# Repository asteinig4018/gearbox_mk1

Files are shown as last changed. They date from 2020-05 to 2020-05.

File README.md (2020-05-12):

# Gearbox Project (featuring snap fits)

Just a simple 3D printed gearbox to be used with my TM 9V Arduino kit motor. Gears down the high speed to a potentiometer - compatible speed.

## Motivation

I wanted to use a 9V TM motor with a 10K ACP Potentiometer (180 degrees of rotation). 
I was hopping to put something physical with the Arduino PID library. 
I also wanted to explore 3D printed snap fits and gears.
And, finally, write better README's.

## Features

### Snap Fits

Snap Fit Demo

The snap fits are designed to fit 5mm holes. The ones I printed with 20% infill PLA can be removed without damaging the mechanism. 

### Gears

All gear are metric module 1.5 spur gears with a 7.5 cm hex bore. Each gear interacts with 5 mm of height.

### Gearing

This is a 6-stage gearbox with a total ratio of 3918.75:1.
A second output exists after the second stage with a ratio of 16.5:1

| Stage | Gears | Ratio | Cummulative Ratio |
| --- | --- | --- | --- |
| 1 | 33:10 | 3.3:1 | 3.3:1 |
| 2 | 50:10 | 5:1 | 16.5:1 |
| 3 | 50:10 | 5:1 | 82.5:1 |
| 4 | 50:10 | 5:1 | 412.5:1 |
| 5 | 50:10 | 5:1 | 2062.5:1 |
| 6 | 19:10 | 1.9:1 | 3918.75:1 |

## Development

### Constraints

The primary constraint was the 180 degree limit on the potentiometer. Beyond that, all parts needed to fit the bed of my 3D printer and, ideally, not take ages to print.

### SolidWorks

SolidWorks Render:

Gearbox Solidworks - Render

All parts were modeled in SolidWorks in metric. 
As the gear models are based off toolbox components, these need to opened before the assembly to prevent SolidWorks from referencing the wrong parts. 

### 3D Printing

All parts were printed on my custom Prusa Mk2 - similar 3D printer with 20% infill. 

### Electronics

All control is done via an Arduino UNO. The 9V from a battery are used with an L293DNE H-bridge. The ACP potentiometer takes 5V and ground with the slider pin going into one of the Arduino's ADCs.

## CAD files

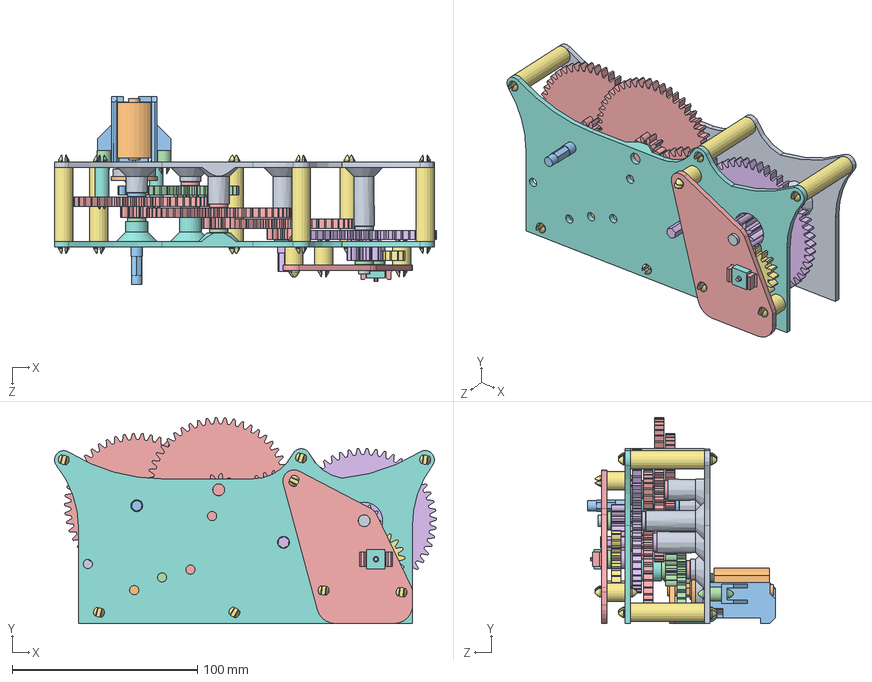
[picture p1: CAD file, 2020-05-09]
gear_box_asm.SLDASM
206.0 x 111.1 x 101.4 mm
motor_engagement
engagement_adapter
metric_gear_10_hex
metric_gear_30_hex
metric_gear_50_hex x 3
metric_gear_50_hex_extralong
metric_gear_19_hex
back_side
front_side
engagement_support
long_axle
small_washer x 5
small_axle x 2
fourth_stage_axle
snap_fastner x 6
snap_fastner_short x 2
fifth_stage_axle
motor
motor_support
snap_fastner_motor x 2
output_support
pot_axle
output_snap_fastner x 3
pot_simplified

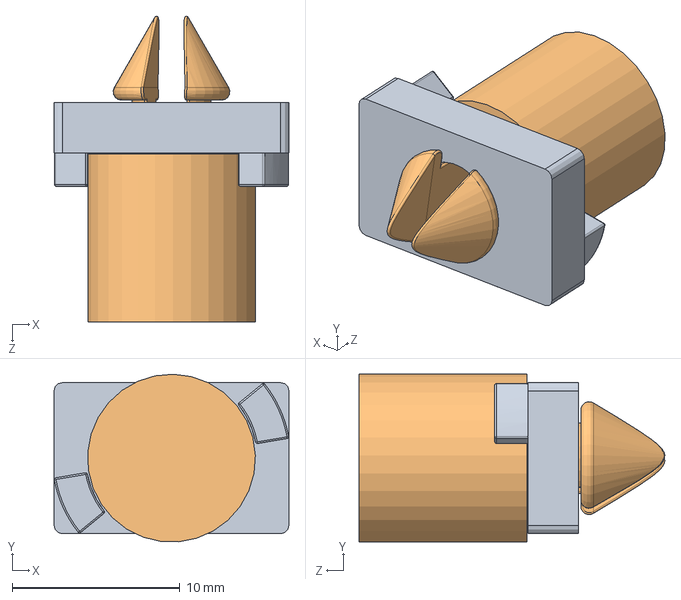
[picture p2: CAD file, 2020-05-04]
snap_fit_test/snapper_v1.SLDASM
14.0 x 9.98 x 18.2 mm
base
snapper

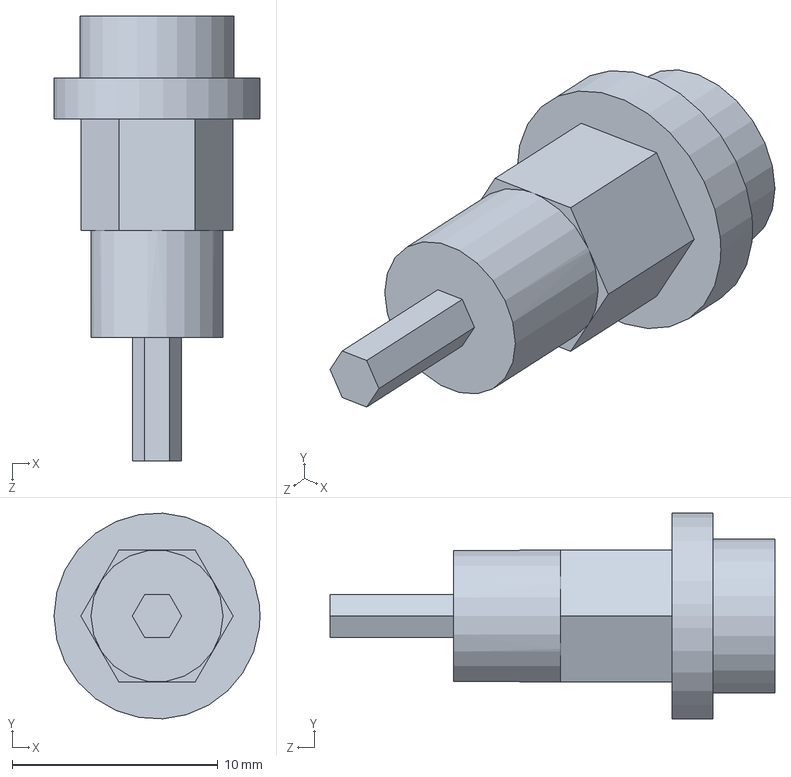
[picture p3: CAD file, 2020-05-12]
pot_axle.SLDPRT
10.0 x 9.98 x 21.6 mm

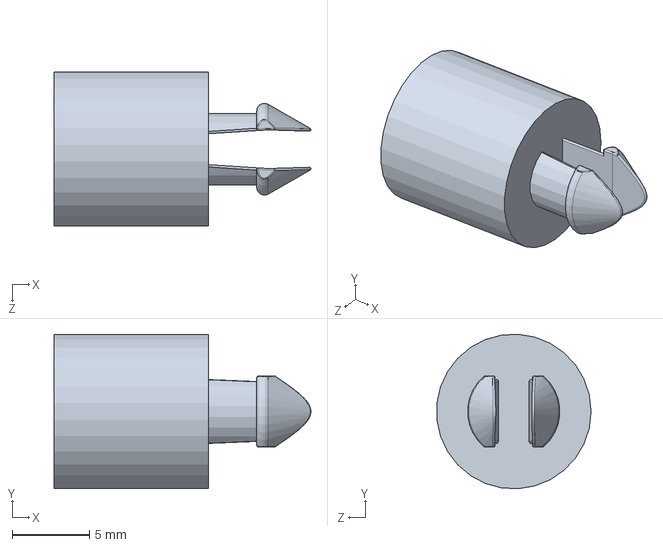
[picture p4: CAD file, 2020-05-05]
snap_fit_test/snapper.SLDPRT
16.6 x 9.99 x 9.97 mm

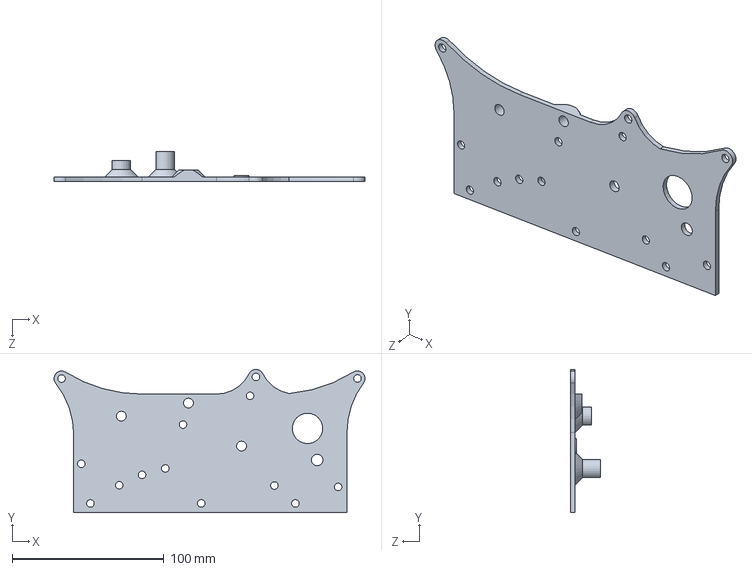
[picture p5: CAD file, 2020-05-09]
back_side.SLDPRT
204.8 x 94.3 x 19.7 mm

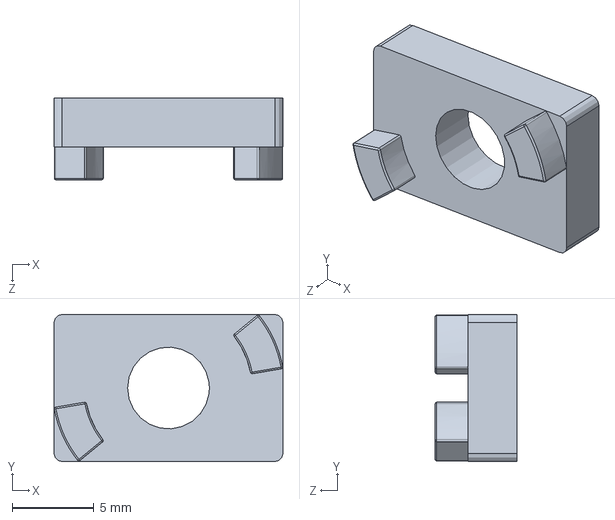
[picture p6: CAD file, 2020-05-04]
snap_fit_test/base.SLDPRT
14.0 x 9.00 x 5.00 mm

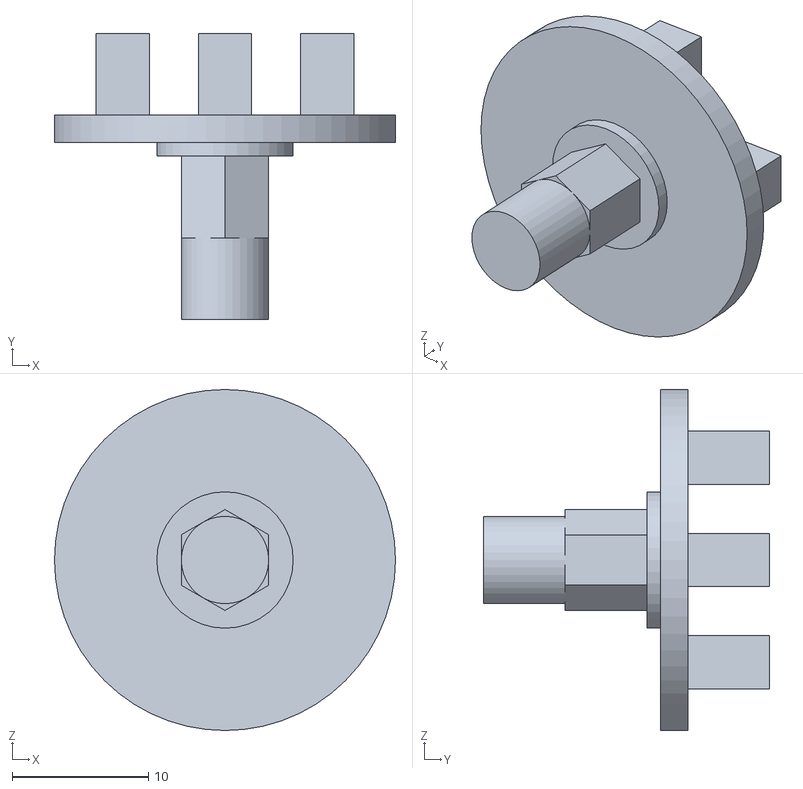
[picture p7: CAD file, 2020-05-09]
stls/engagement_adapter_v3.STL
25.0 x 21.0 x 25.0

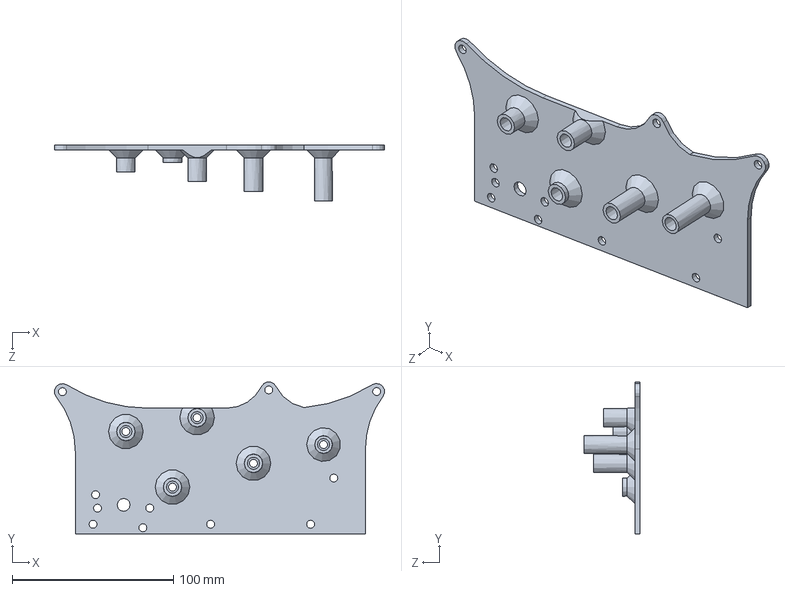
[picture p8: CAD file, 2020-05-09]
front_side.SLDPRT
204.7 x 94.2 x 34.7 mm

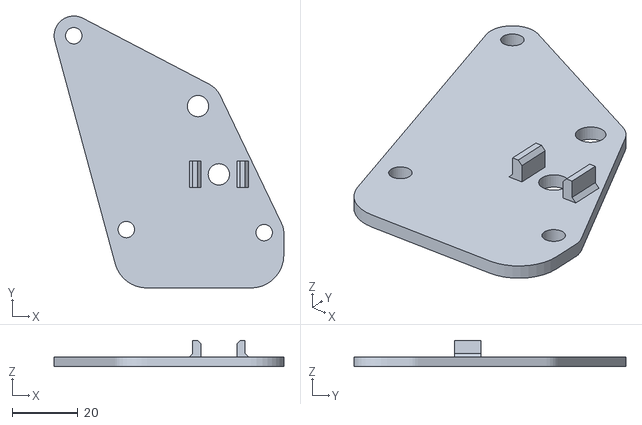
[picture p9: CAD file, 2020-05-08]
stls/output_support_v1.STL
70.0 x 82.9 x 8.00

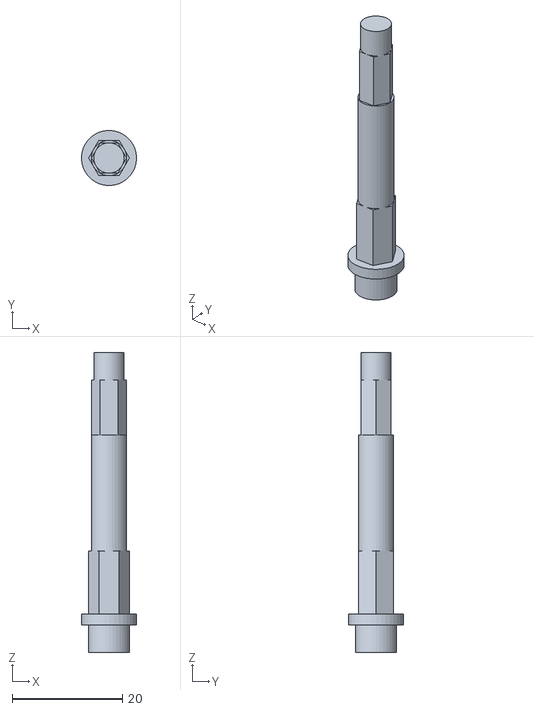
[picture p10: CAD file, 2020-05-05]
stls/long_axle_v1.STL
10.0 x 10.0 x 54.4

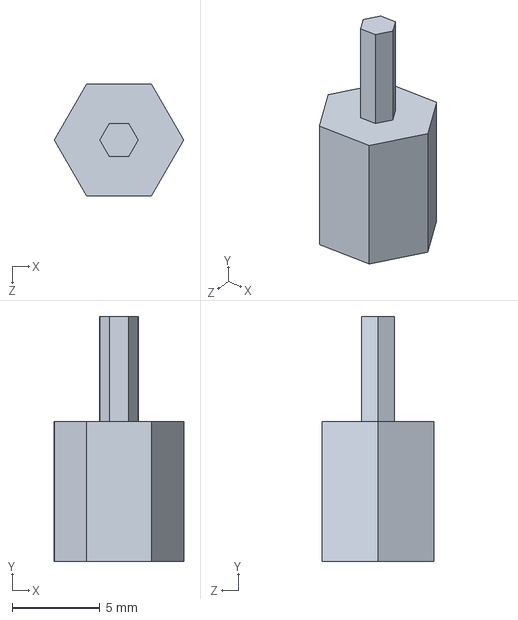
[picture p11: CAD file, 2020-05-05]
pot_engagement_tester.SLDPRT
7.40 x 14.0 x 6.41 mm

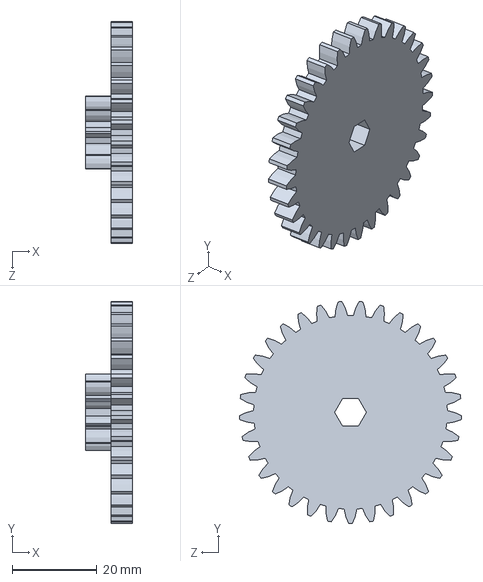
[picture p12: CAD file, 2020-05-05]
metric_gear_30_hex.SLDPRT
11.0 x 52.4 x 52.5 mm

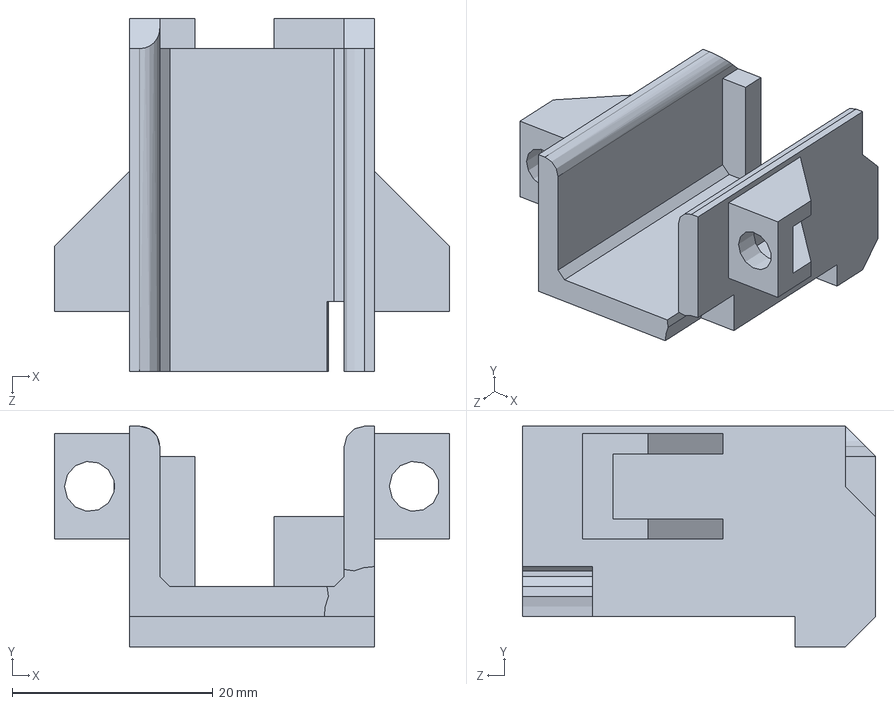
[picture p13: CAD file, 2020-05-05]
motor_support.SLDPRT
39.4 x 22.0 x 35.2 mm

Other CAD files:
snap_fit_test/stls/snapper_v2.STL
stls/pot_axle_v3.STL
engagement_adapter.SLDPRT
stls/front_side_v2.STL
output_support.SLDPRT
engagement_support.SLDPRT
fifth_stage_axle.SLDPRT
fourth_stage_axle.SLDPRT
long_axle.SLDPRT
metric_gear_10_hex.SLDPRT
metric_gear_19_hex.SLDPRT
metric_gear_50_hex.SLDPRT
metric_gear_50_hex_extralong.SLDPRT
motor.SLDPRT
motor_engagement.SLDPRT
output_snap_fastner.SLDPRT
pot_simplified.SLDPRT
small_axle.SLDPRT
small_washer.SLDPRT
snap_fastner.SLDPRT
snap_fastner_motor.SLDPRT
snap_fastner_short.SLDPRT
snap_fit_test/stls/base.STL
snap_fit_test/stls/snapper.STL
stls/back_side_v1.STL
stls/engagement_adapter_v1.STL
stls/engagement_adapter_v2.STL
stls/engagement_support_v1.STL
stls/fifth_stage_axle_v1.STL
stls/fourth_stage_axle_v1.STL
stls/front_side_v1.STL
stls/metric_gear_10_hex_v1.STL
stls/metric_gear_19_hex_v1.STL
stls/metric_gear_30_hex_v1.STL
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

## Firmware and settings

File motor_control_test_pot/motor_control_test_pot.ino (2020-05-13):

/**
 * This test turns the motor each direction 
 * while measuring its position with the pot.
 * It will ignore up to 5 false readings by the 
 * pot.
 */
const int controlPin1 = 2;
const int controlPin2 =3;
const int enablePin = 9;

const int buttonPin = 5;

const int posPotPin = A1;

void setup() {
  // put your setup code here, to run once:
  pinMode(controlPin1, OUTPUT);
  pinMode(controlPin2, OUTPUT);
  pinMode(enablePin, OUTPUT);

  digitalWrite(enablePin, LOW);

  Serial.begin(9600);

}

void loop() {
  // put your main code here, to run repeatedly:
  //on button press
  delay(100);
  int x = 1;
  //if(digitalRead(buttonPin) == HIGH){
  if(x == 1){
    x = 0;
    int startPos = analogRead(posPotPin);
    digitalWrite(controlPin1, HIGH);
    digitalWrite(controlPin2, LOW);

    analogWrite(enablePin, 255);

    int disconnects = 0;

    bool endReached = false;
    while(!endReached){
      int currentPos = analogRead(posPotPin);
      //if disconnect happens once 
      if(abs(currentPos - startPos)>100 &&
        disconnects < 5){
          disconnects ++;
          Serial.println("Error");
          //ignore
        }
       else if(currentPos < 200){
        analogWrite(enablePin, 0);
        endReached = true;
        //stop once destination is reached
       }
       else if(disconnects >= 5){
        Serial.println("DISCONNECT ERROR");
        endReached = true;
       }
       Serial.println(currentPos);
       delay(10);
    }

    Serial.println("End reached");
    delay(100);
    
     
    //and now back
    startPos = analogRead(posPotPin);
    digitalWrite(controlPin1, LOW);
    digitalWrite(controlPin2, HIGH);

    analogWrite(enablePin, 255);

    disconnects = 0;

    endReached = false;
    while(!endReached){
      int currentPos = analogRead(posPotPin);
      //if disconnect happens once 
      if(abs(currentPos - startPos)>100 &&
        disconnects < 5){
          Serial.println("ERROR");
          disconnects ++;
          //ignore
        }
       else if(currentPos > 800){
        analogWrite(enablePin, 0);
        analogWrite(controlPin1, LOW);
        analogWrite(controlPin2,LOW);
        endReached = true;
        //stop once destination is reached
       }
       else if(disconnects >= 5){
        Serial.println("DISCONNECT ERROR");
        endReached = true;
       }
       startPos = currentPos;
       Serial.println(currentPos);
       delay(10);
       
    }
    Serial.println("End Reached");
  }
}

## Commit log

2020-05-01 added motor engagement part
    [motor_engagement.SLDPRT]
2020-05-01 added center hole
    [motor_engagement.SLDPRT]
2020-05-02 added main gearbox assembly and gear engagement adapter
    [engagement_adapter.SLDPRT, gear_box_asm.SLDASM]
2020-05-02 added two custom hex hole metric gears 5mm external hex center hole module 1.5
    [metric_gear_10_hex.SLDPRT, metric_gear_30_hex.SLDPRT]
2020-05-02 edited main assembly 30 and 50 custom gears have a 10 attached pitch diameter = #teeth * module #
    [gear_box_asm.SLDASM, metric_gear_30_hex.SLDPRT, metric_gear_50_hex.SLDPRT]
2020-05-03 added stl folder parts ready for 3d printing currently contains a tester part one side should fit the pot, the other side just shows me the size of the axles
    [pot_engagement_tester.STL]
2020-05-03 number of new parts: 19t gear for the final stage that connects to the pot extra long 50t -10t gear combo to reach through the plate to the supported 19t side plates (initial versions) tester parts
    [front_side.SLDPRT, gear_box_asm.SLDASM, metric_gear_19_hex.SLDPRT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]
2020-05-04 added snap fit test folder an initial test of snap fits to be utilized on axles and other points within the gearbox This subproject contains its own stl folder
    [base.SLDPRT, base.STL, snapper.SLDPRT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]
2020-05-04 edited pot engagement adapter following test print of previous stl changed small pot hex from 0.85 to 1mm side length changed larger axle from 5mm to 7.5mm outer circle
    [pot_engagement_tester.SLDPRT, pot_engagement_tester_v2.STL]
2020-05-04 changed pot engagenment adapter to have a longer length still v2, not yet print tested
    [pot_engagement_tester.SLDPRT, pot_engagement_tester_v2.STL]
2020-05-04 updated snapping tester based on print decreased overhang from 1.5 to below 1mm increased outer most split distance cut off tips of snapper not made smaller by bending into the split
    [snapper.SLDPRT, snapper_v2.STL]
2020-05-04 updated to v3 of pot engagement tester based on print smaller hex is still not large enough, increased to 1.2mm side length decreased larger hex to 7.4 circle for more realistic engagement size
    [pot_engagement_tester.SLDPRT, pot_engagement_tester_v3.STL]
2020-05-04 updated pot_engagement adapter to newest dimension based on last print This dimension should work. I'm not going to test it. If the final part needs some adjustment, I'll file or reprint that one.
    [pot_engagement_tester.SLDPRT]
2020-05-04 updated snapper test piece based on latest print. Print worked, but minor adjustment will limit further post processing
    [snapper.SLDPRT]
2020-05-04 updated all parts for a new 7.5mm outer circle hex shaft created stls for the 10t gear and the engagenement adapter
    [engagement_adapter.SLDPRT, engagement_adapter_v1.STL, gear_box_asm.SLDASM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]
2020-05-04 updated engagement adapter based on print tolerances updated slightly for a tighter fit. Good over all though
    [engagement_adapter.SLDPRT]
2020-05-05 large update to mostly complete gearbox both panels updated for support points. Snap fastener created and added panels updated to hold axles. Axles created and placed. Engagement support panel create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
    [back_side.SLDPRT, engagement_adapter.SLDPRT, engagement_adapter_v2.STL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]
2020-05-05 added motor support parts and mount
    [engagement_support.SLDPRT, front_side.SLDPRT, gear_box_asm.SLDASM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]
2020-05-05 updated for output stage and pot mounting added mounting plate and necessary snap fasteners
    [back_side.SLDPRT, fifth_stage_axle.SLDPRT, fourth_stage_axle.SLDPRT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]
2020-05-05 updated back side plate with mounting holes for future additions ie. more stages or something on the output
    [back_side.SLDPRT, gear_box_asm.SLDASM]
2020-05-05 first wave of stls to be printed in blue. Side plates will be black. still need some axles and fasteners
    [front_side.SLDPRT, gear_box_asm.SLDASM, metric_gear_30_hex.SLDPRT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]
2020-05-05 remaining stls have been generated
    [back_side_v1.STL, fifth_stage_axle_v1.STL, fourth_stage_axle_v1.STL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]
2020-05-05 updated front side motor pass through hole to allow pinion gear to pass through
    [front_side.SLDPRT, front_side_v2.STL]
2020-05-08 added output support stl also updated output support to have fillets on the corners
    [output_support.SLDPRT, output_support_v1.STL]
2020-05-08 updated pot axle for shorter length due to contact
    [pot_axle.SLDPRT, pot_axle_v2.STL]
2020-05-09 updated assembly
    [gear_box_asm.SLDASM]
2020-05-09 updated engagement adapter for more accurate motor dimensions
    [back_side.SLDPRT, engagement_adapter.SLDPRT, engagement_adapter_v3.STL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]
2020-05-12 updated pot axle for larger hex hopefully will reduce backlash in pot
    [pot_axle.SLDPRT, pot_axle_v3.STL]
2020-05-12 updated README with many more details added gifs for readme added some arduino code
2020-05-13 added more arduino testing code
